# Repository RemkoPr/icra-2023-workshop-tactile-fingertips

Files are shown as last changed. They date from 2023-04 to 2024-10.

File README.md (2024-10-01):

# ICRA2023 Transferability in Robotics Workshop 
## Augmenting Off-the-Shelf Grippers with Tactile Sensing
[Paper](https://doi.org/10.48550/arXiv.2306.05902) -- [Related work](https://doi.org/10.1109/LRA.2023.3284382)

The development of tactile sensing ad its fusion with computer vision is expected to enhance robotic systems in handling complex tasks like deformable object manipulation. However, readily available industrial grippers typically lack tactile feedback, which has led researchers to integrate and develop their own tactile sensors. This has resulted in a wide range of sensor hardware and difficulty in comparing tasksolving performance. We propose moving towards accessible open-source sensors and present a set of fingertips specifically designed for fine object manipulation, with readily interpretable data output. The fingertips are validated through two difficult tasks: cloth edge tracing and cable tracing. 

## Video material
Video material of the proof-of-concept experiments is provided in the videos folder.

## Hardware integration

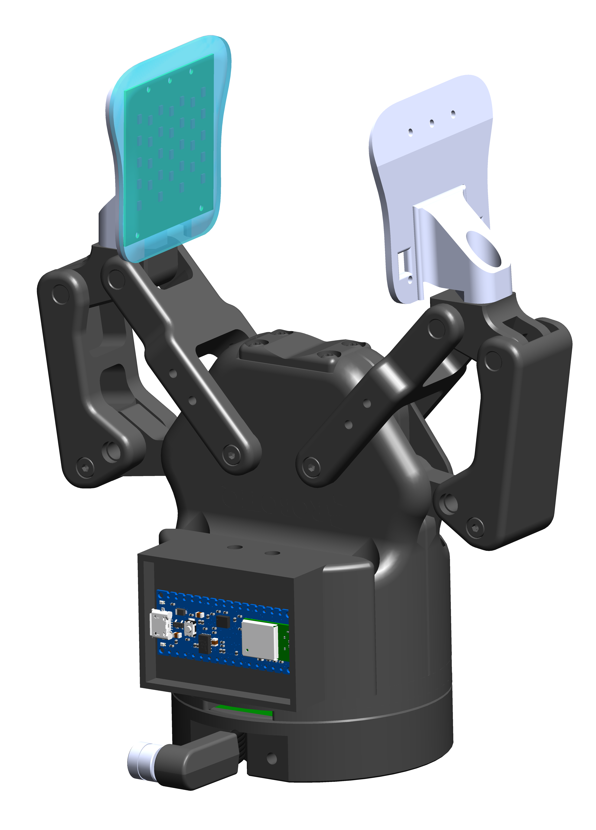
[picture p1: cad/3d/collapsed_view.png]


Currently the fingertips are designed for the Robotiq-2F85 gripper. This gripper can be mounted to various different collaborative robot arms by means of a tool flange. We provide a design for an intermediate flange, nestled between the Robotiq tool flange and the gripper itself, that provides external interfaces for the supply and ground pins otherwise reserved for the gripper. This way, the sensorised fingertips can draw their power straight from the robot arm. The intermediate flange consists of a pcb in the cad/pcb folder and two 3D printed parts in the cad/3d folder. Sensor readout is currently performed by an Arduino Nano 33 BLE externally mounted to the gripper via a 3D printed holder (see cad/3d), but we are in the process of integrating a microcontroller on our custom intermediate flange such that sensor readout and data transmission can also be done internally.  

<BR CLEAR="all">

## Software integration
Both Arduino firmware and python readout software is provided. Data is communicated between the arduino and a remote workstation via Bluetooth Low Energy. Further documentation on the software is provided in the code/python folder.

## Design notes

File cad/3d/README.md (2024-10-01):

This folder contains 3D CAD designs. The solidworks folder contains .sldprt and .sldasm files for editing in SolidWorks. The stl folder contains .stl files for 3D printing without adjustments. The fingertips come in two versions, rigid and flexible. 

The rigid version (IRTouch_rigid) is a single part, best printed face-side up, so that the PCB slot remains smooth. The flex version consists of two parts, where the mechanical interface (IRTouch_flex_interface) is best printed in rigid material. The other part (IRTouch_flex) is printed with Flexfil 98A, face side down, so no support is needed. 

### Note
The files 2F85-OPENED-NO_FINGER.SLDASM and IO_20Coupling_20UR_20CB_20190807.SLDPRT are pulled straight from the [Robotiq Downloads page](https://robotiq.com/cobot-brands/universal-robots).


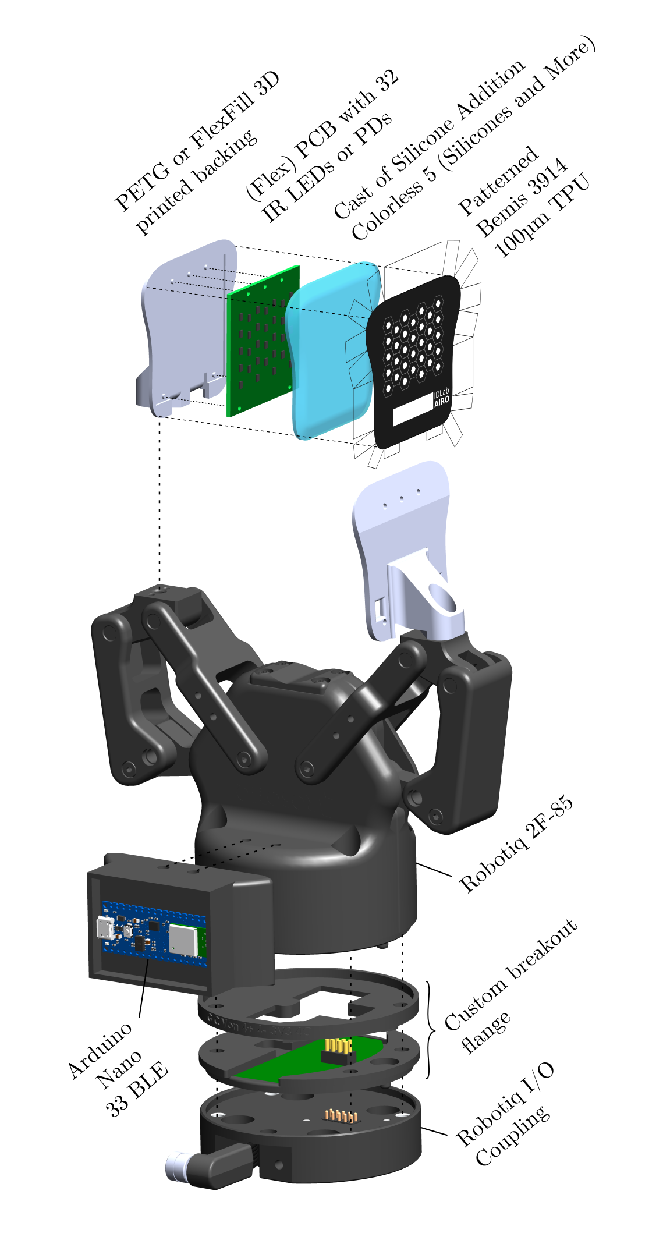
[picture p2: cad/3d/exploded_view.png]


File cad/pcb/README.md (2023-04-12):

This folder contains PCB design files for both the receiver (irtouch_led) as well as the tranmitter (irtouch_rcv) tactile finger. Additionally, the design for the custom breakout flange (robotiq_wrist_coupling) PCB is provided. This PCB is set between the Robotiq I/O Coupling and the 2F-85 gripper itself. The arduino_breakout is a simple PCB to which female 0.1" pin headers are soldered. This PCB fits in the Arduino_holder found in cad/3d.

Refer to the cad/3d folder for an exploded view of the structural integration.

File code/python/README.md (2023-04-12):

# SensorComm

Package allowing communication with IRTouch infrared tactile fingertips, read out using an Arduino nano 33 BLE via Bluetooth Low Energy.

Install using 
```
pip install -e path-to-package-root
```

You may need to install the [TKinter](https://riptutorial.com/tkinter/example/3206/installation-or-setup) module separately. It might be pre-installed, but only for Python2, so make sure it is installed for Python3.
## Note
There's an issue where, if the BLE data characteristic UUID is changed in the Arduino firmware after having already connected to the python script using a different UUID, python may not be able to recongize the new UUID, requiring you to use the old UUID.

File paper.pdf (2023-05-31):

# Augmenting Off-the-Shelf Grippers with Tactile Sensing

1

st Remko Proesmans
IDLab-AIRO
Ghent University – imec
Ghent, Belgium
Remko.Proesmans@UGent.be

2

nd Francis wyffels
IDLab-AIRO
Ghent University – imec
Ghent, Belgium
Francis.wyffels@UGent.be

Abstract—The development of tactile sensing and its fusion with computer vision is expected to enhance robotic systems in handling complex tasks like deformable object manipulation. However, readily available industrial grippers typically lack tactile feedback, which has led researchers to develop and integrate their own tactile sensors. This has resulted in a wide range of sensor hardware, making it difficult to compare performance between different systems. We highlight the value of accessible open-source sensors and present a set of fingertips specifically designed for fine object manipulation, with readily interpretable data outputs. The fingertips are validated through two difficult tasks: cloth edge tracing and cable tracing. Videos of these demonstrations, as well as design files and readout code can be found at https://github.com/RemkoPr/icra-2023-workshop-tactile-fingertips. (https://github.com/RemkoPr/icra-2023-workshop-tactile-fingertips)
Index Terms—Tactile sensing, Sensor-based Control, Open-source
I. INTRODUCTION

Deformable object manipulation challenges several assumptions of classical robotics, like object rigidity, a lowdimensional state space and known dynamics models [1]. Tactile sensing and its fusion with computer vision is expected to strengthen robotic systems in dealing with such complex deformable objects [2]. However, commercially available industrial grippers typically do not feature tactile feedback [3], [4]. At most, binary object detection is included such that delicate parts can be grasped without exerting maximal gripping force. This, combined with force torque sensing in the joints of a robotic arm, is the current extent of readily available tactile feedback. Hence, researchers are required to integrate and even develop their own tactile sensors. Sensor technologies in literature include piezoresistive [5], capacitive [6], thermoelectric [7], optoelectronic [8] and more. This heterogeneity in sensor hardware makes it difficult to compare the performance of control algorithms as the nature of the sensor is strongly intertwined with any control algorithm exploiting it. Few dedicated robotic tactile sensor platforms have been adopted outside their founding research groups. The emphasis of systems that do achieve external adoption, such as robot skins like uSkin [9] and tactile fingertips like GelSight [10],

Remko Proesmans is a predoctoral fellow of the Research Foundation Flanders (FWO) under grant agreement no. 1S15923N. This work was also partially supported by the euROBIn Project (EU grant number 101070596).

is transferability between robotic platforms. These systems aim to be fit for a variety of robots and robotic grippers, so that researchers can acquire tactile add-ons to their pre-owned robotic infrastructure. This hardware transferability facilitates task transferability, mitigating the issue of benchmarking in experiments making use of tactile sensing. GelSight sensors, however, come with considerable overhead in terms of data processing and hardware integration, the latter being due to external cable routing. We argue that there is plenty of room for accessible, open-source tactile fingertips with readily interpretable data outputs. We present a set of narrow fingertips specifically suited for narrow object manipulation and demonstrate their potential in two actively explored problems in the state-of-the-art: cloth edge tracing [11] and cable tracing [8], [12].

II. TACTILE SENSING FOR NARROW OBJECTS

A. Electrical sensor design
The tactile fingers are two complementary designs: one finger emits infrared (IR) light, the other receives it. The fingertips are integrated on a Robotiq 2F-85 gripper, mounted on a UR3e collaborative robot arm. Fig. 1 shows the schematic of the integrated system. The first finger contains a grid of 32 IR light-emitting diodes (LEDs), connected in two parallel branches of each sixteen LEDs. The grid is supplied directly by the 24 V output of the UR3e arm via custom breakout flange between the Robotiq I/O Coupling and the gripper itself. Note that the I/O Coupling, and thus our sensor system, fits a multitude of different cobots and Robotiq grippers. The LED finger consumes 40 mA after a warmup time of five minutes. The second finger consists of 32 IR photodiodes (PDs). Here, four demultiplexers (DEMUX) are included, each addressing eight PDs. The DEMUX are all simultaneously controlled by three digital pins of an Arduino Nano 33 BLE, such that they each route one of four analog pins to one of eight of their respective PDs. In future work, a microcontroller will be integrated on the breakout flange, replacing the externally mounted Arduino. The second finger consumes about 1 mA of current from the 3.3 V output of the Arduino, which in turn receives its power from the 24 V UR3e tool output converted to 5 V by a switching regulator on the breakout flange. The discussed electrical specifications are summarised in Table I.

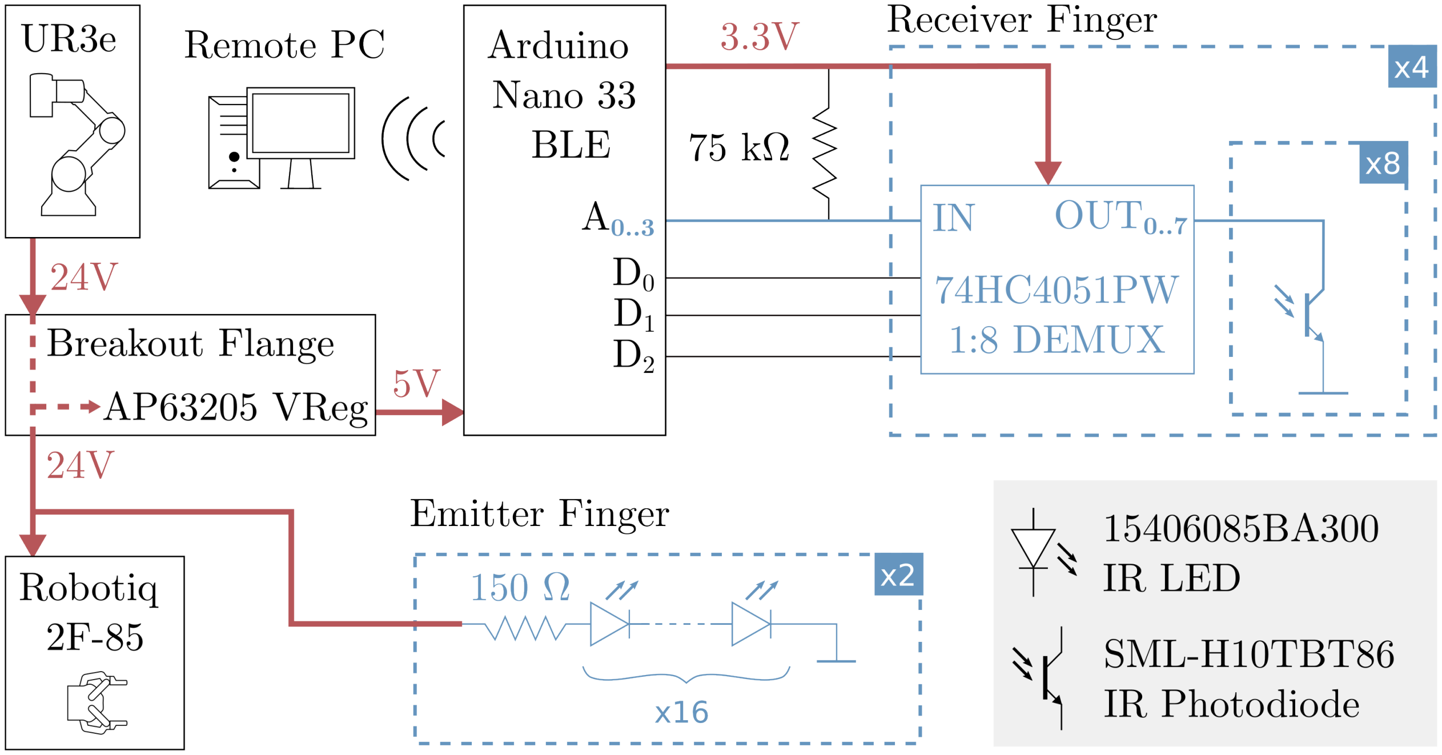
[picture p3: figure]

Fig. 1: Electrical diagram of the tactile fingers integrated on a UR3e.

TABLE I: Technical specifications of the tactile fingers.

Characteristic | Value
Total current consumption (incl. readout) | 45 mA
Receiver finger | 1 mA
Emitter finger | 38 mA
Warmup time | 5 min
Physical size (width × height × depth) | 58.0 × 54.0 × 21 mm³
PCB dimensions | 42.8 × 43.1 mm²
Sensorised area | ∼38.0 × 30.0 mm²
Thickness excluding gripper coupling | 4.0 mm
Sensor density | 3.21 cm⁻²
Data resolution | 8 bit
Readout frequency | 55 Hz

The total current consumption reported includes the voltage regulator and the Arduino during readout.

B. Structural sensor design & manufacturing Structurally, both tactile fingers are largely similar. Fig. 2 shows their constituent parts. The IR LEDs and PDs are each placed in an identical hexagonal grid on their respective printed circuit boards (PCBs), such that a single LED is located straight across from a single PD when both fingers are brought close together. For each finger, the PCB is slotted into a polyethylene terephthalate glycol (PETG) backing, 3D printed using a Prusa MK3 i3. Alternatively, we have succeeded in producing a compliant version by printing the backing with Flexfill TPU 98A and using a flexible PCB. The resulting structure is placed PCB side down into a mould filled with liquid Silicone Addition Colorless 5 obtained from Silicones and More. After curing at room temperature for 24 hours, the finger is removed from the mould and a 1 mm layer of translucent silicone protects the PCB components. We have, however, observed degradation in the polymer right above the IR LEDs after ∼100 grasp cycles, so further material exploration is warranted. However, the surface of this silicone layer is sticky and easily accumulates dirt. Hence, a sheet of 100 µm thick Bemis 3914 thermoplastic polyurethane (TPU) is shaped around the combined PETG, PCB and silicone structure by pulling the TPU taut and heating it locally using a CIF 852 hot air gun set to 90 °C. The TPU was found to provide a low-friction surface for cloth manipulation and is highly

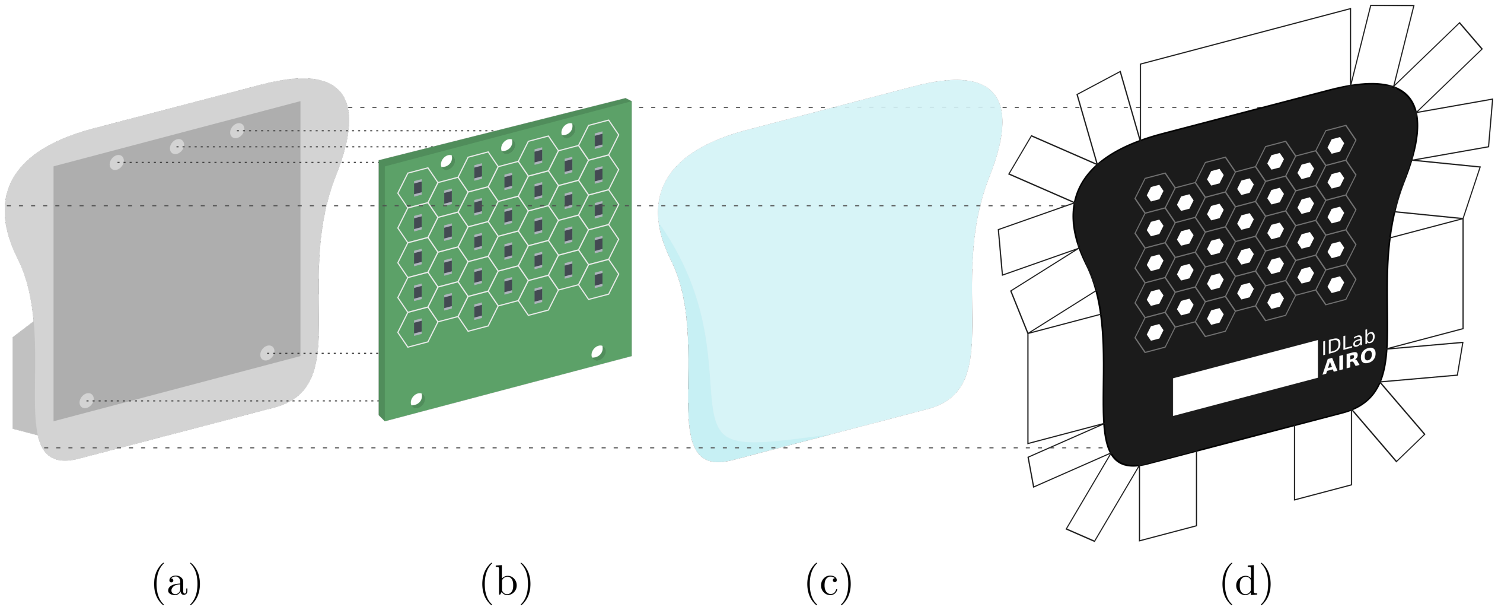
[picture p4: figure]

Fig. 2: Sensor structure for both the emitting as well as the receiving finger. (a) 3D printed PETG backing. (b) PCB, either with 32 IR LEDs or 32 IR PDs. (c) 1.5 mm thick layer of translucent silicone. (d) Sheet of 100 µm Bemis 3914 TPU patterned with black ink.

durable during normal use. Additionally, before shaping, a hole pattern is printed in black on the inside of the TPU layer using an HP LaserJet P2015. Each hole is positioned directly above an IR emitter or receiver, thus focusing their respective radiation patterns. The entire fingertip is 4 mm thick and has a slanted tip, making it suitable for sliding underneath cloth for grasping, as opposed to e.g. GelSight sensors [10]. Table I provides additional structural specifications.

C. Sensor readout
Getting a single readout from the tactile fingers entails sequentially setting the common selection inputs for the DE-MUX to one of eight codes and reading the voltage on the four analog pins that are routed along the receiver grid. This data is transmitted in an 8-bit format at about 55 Hz by the Arduino over Bluetooth Low Energy (BLE). Wireless communication avoids cable routing and thus reduces integration overhead. The use of a widespread communication protocol further encourages transferability.
When the fingers are close together, the PDs receive high IR intensity and pull down the analog pins to ground. Grasped objects between the fingers block a large part of the IR light from the LEDs, which leads to the PDs conducting less and results in higher voltages read by the analog pins. This sensing principle is specifically suited towards, but not limited to, detecting exceedingly narrow objects. Thin cloth, for example, is tough to detect using traditional force sensors. In the following, the 8-bit complement of the readings is reported, as it is more intuitive that high IR light transmission corresponds to high sensor readings.

III. EXPERIMENTAL VALIDATION

A. Response to different materials
The sensor readout depends on the translucency of the material that is grasped. Fig. 3 shows the average 8-bit value received by the PD grid when placing different materials between the fingertips at a separation distance of 6 mm. The materials are solid cardboard, a pink hand towel, a sheet of white paper, a thin white cloth napkin and a clear plastic ziplock bag. The results are intuitively clear: more translucent materials lead to higher sensor readings.

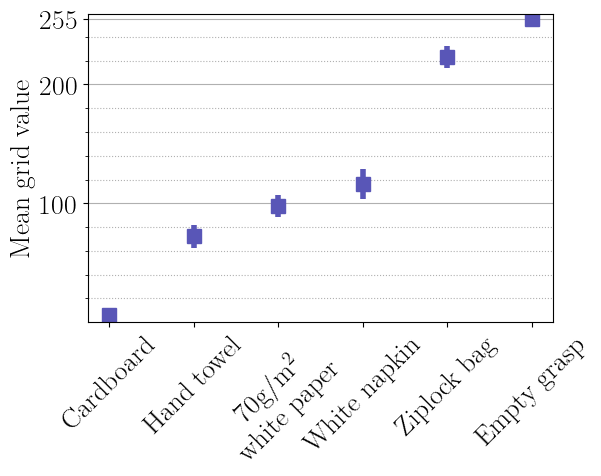
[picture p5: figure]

Fig. 3: Mean sensor values when grasping different materials.

B. Task solving

The sensors are validated in two actively explored problems in the state-of-the-art: cloth edge tracing (Fig. 4a-4d) and cable tracing (Fig. 4e-4f). The used methods are directly transferable to other robotic installations to which the fingertips can be fitted. We refer the reader to the accompanying GitHub page for video material.
The tactile data is distilled into a set of control parameters as follows. Each data value corresponds to a hexagonal cell, of which the position in the grid is defined by its centre coordinates. In most use cases, the grid will show distinct dark and bright zones, see the visualisations in Fig. 4. Several processing steps are applied to the sensor data:
- The threshold λ deciding which values are “bright”, respectively “dark”, is calculated by sorting all grid values from lowest to highest and finding the largest step between adjacent values. Any values found before this step are “dark”, the others “bright”. λ is then set to the average of the bright cluster mean and the dark cluster mean value.
- The centre point of the dark cluster is calculated as the weighted mean of the centre coordinates of all cells belonging to the dark cluster, where the weights are the 8-bit complements of the associated values.
- The shape of the border between the dark and the bright cluster indicates whether or not a corner is grasped when tracing cloth, or shows the angle at which the cable is passing through the fingers. To find the border shape, the value of each cell is compared to those of the neighbouring cells. If λ is crossed between cells, the values of the cells are linearly interpolated along the line segment connecting the cell centre points and an edge marker is placed where an interpolated value of λ is found. Piecewise linear functions are then fitted to these edge markers.

In both experiments, proportional control with manually tuned gain is used to maintain the centre point of the dark cluster at a certain height in the sensor grid.

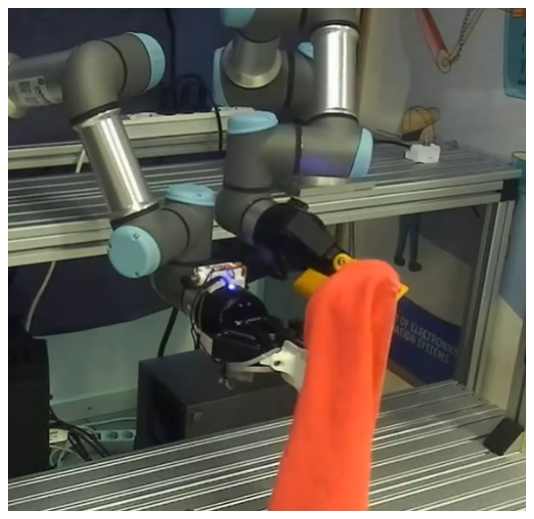
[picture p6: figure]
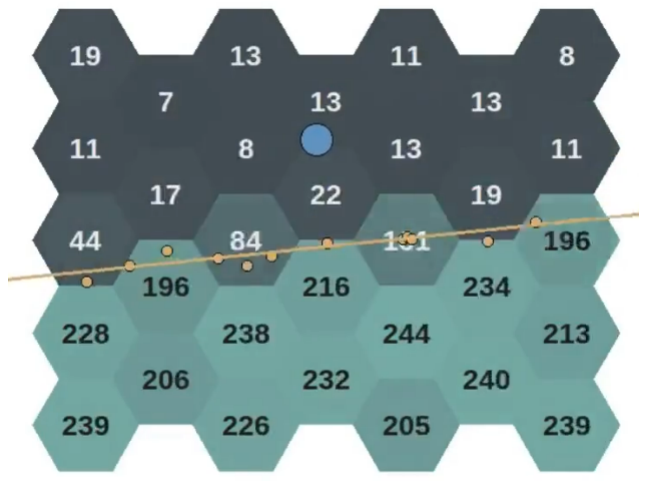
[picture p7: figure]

(a) Grasping cloth edge. (b) Sensor values corresponding to Fig. 4a.

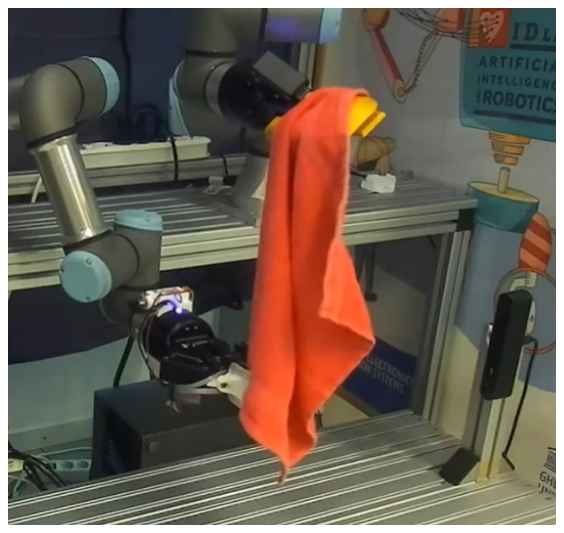
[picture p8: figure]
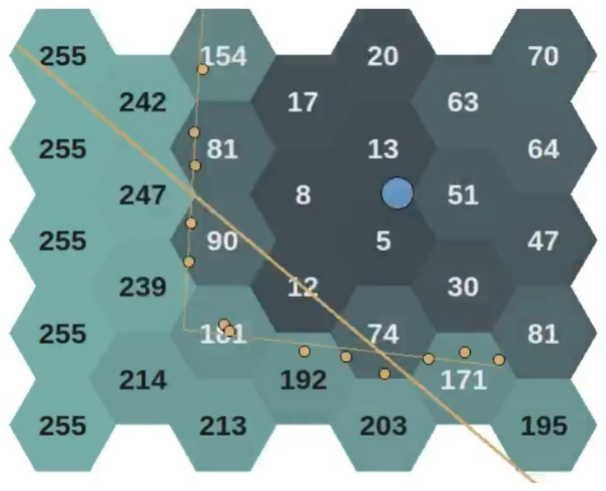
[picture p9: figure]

(c) Grasping cloth corner. (d) Sensor values corresponding to Fig. 4c.

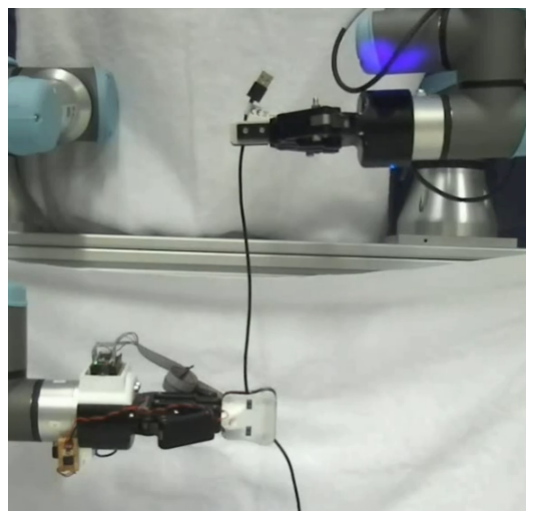
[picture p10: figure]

(e) Grasping 3 mm USB cable.

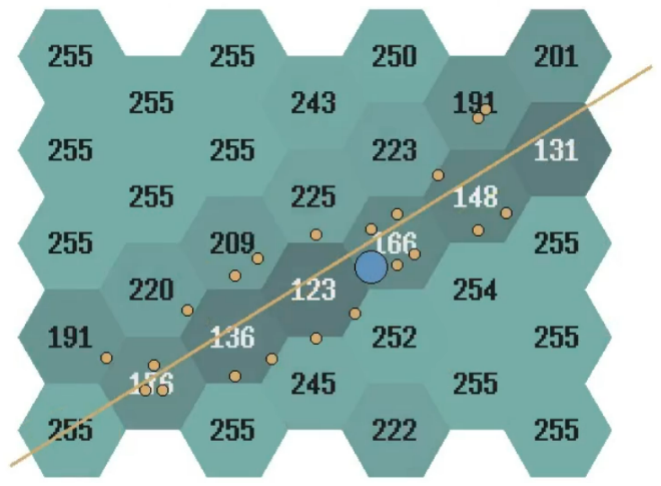
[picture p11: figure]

(f) Sensor values corresponding to Fig. 4e.

Fig. 4: Cloth and cable tracing.

IV. CONCLUSION

Transferability in robotics is strongly hardware-limited. In the field of tactile sensing, a mitigating approach is to design tactile fingertips, facilitating transfer of such sensors between heterogeneous robotic hardware and potentially allowing for direct control policy transferability. We have presented a set of open-source optoelectronic tactile fingertips and have demonstrated their potential in cable and cloth edge tracing. The tactile fingertips are uniquely suited towards manipulation of narrow objects, while being thinner than e.g. GelSight sensors and the optoelectronic sensors in [8], allowing for a compliant design. Additionally, sensor platforms like ours are more accessible than GelSight sensors in terms of cost and both hardware and software integration, further incentivising benchmarking in tactile robotics.

REFERENCES

[1] J. Zhu et al., ”Challenges and Outlook in Robotic Manipulation of Deformable Objects,” in IEEE Robotics & Automation Magazine, vol. 29, no. 3, pp. 67-77, Sept. 2022.
[2] A. Billard, and D. Kragic, ”Trends and challenges in robot manipulation,” in Science, vol. 364, no. 6446, pp. eaat8414, June 2019.
[3] J. Borras, G. Aleny ` | a and C. Torras, ”A grasping-centered analysis for `
cloth manipulation,” in IEEE Transactions on Robotics, vol. 36, no. 3, pp. 924-936, June 2020.
[4] L. Birglen, and T. Schlicht, ”A statistical review of industrial robotic grippers,” in Robotics and Computer-Integrated Manufacturing, vol. 49, pp. 88-97, February 2018.
[5] L. Zlokapa et al., ”An integrated design pipeline for tactile sensing robotic manipulators,” International Conference on Robotics and Automation (ICRA), pp. 3136-3142, April 2022.
[6] E. J. K. Judd, B. Aksoy, K. M. Digumarti, H. Shea, and D. Floreano, ”Slip anticipation for grasping deformable objects using a soft force sensor,” in International Conference on Intelligent Robots and Systems (IROS), October 2022.
[7] G. Li, S. Liu, L. Wang, and R. Zhu, ”Skin-inspired quadruple tactile sensors integrated on a robot hand enable object recognition,” in Science Robotics, vol. 5, no. 49, December 2020.
[8] A. Cirillo, M. Costanzo, G. Laudante, and S. Pirozzi, ”Tactile sensors for parallel grippers: design and characterization,” in Sensors, vol. 21, no. 5, p. 1915, March 2021.
[9] T. P. Tomo et al., ”A new silicone structure for uSkin—a soft, distributed, digital 3-axis skin sensor and its integration on the humanoid robot iCub,” in IEEE Robotics and Automation Letters, vol. 3, no. 3, pp. 2584-2591, July 2018.
[10] M. Lambeta et al., ”DIGIT: A novel design for a low-cost compact high-resolution tactile sensor with application to in-hand manipulation,” in IEEE Robotics and Automation Letters, vol. 5, no. 3, pp. 3838-3845, July 2020.
[11] N. Sunil, S. Wang, Y. She, E. Adelson, and A. Rodriguez, ”Visuotactile Affordances for Cloth Manipulation with Local Control,” in Conference on Robot Learning (CoRL), December 2022.
[12] Y. She, S. Wang, N. Sunil, A. Rodriguez, and E. Adelson, ”Cable manipulation with a tactile-reactive gripper,” in Int. J. Robot. Res. (IJRR), vol. 40, no. 12-14, pp. 1385-1401, August 2021.

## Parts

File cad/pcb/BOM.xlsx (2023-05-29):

 | Component | Manufacturer part number | Quantity | PCB designation
Receiver finger
 | infrared photodiode | SML-H10TBT86 | 32 | Q1-32
 | 1-to-8 demultiplexer | 74HC4051PW | 4 | U1-4
 | pull-down resistor | any 75kOhm 0603 1/16W | 4 | R1-4
Transmitter finger
 | infrared LED | 15406085BA300 | 32 | D1-32
 | current limiting resistor | any 150 Ohm 0603 1/10W | 2 | R3, R8
Breakout flange
 | pogo pin header | 827-22-010-10-001101 | 1 | U12
 | 7 position box header | any 90° 2,54mm pitch 7-positiion box header | 2
 | 5V switching regulator | AP63205 | 1 | IC1
 | decoupling capacitor | any 0805 22µF capacitor | 2 | C3, C4
 | decoupling capacitor | any 0603 10µF 30V rated capacitor | 1 | C1
 | decoupling capacitor | any 0603 100nF capacitor | 1 | C2
 | inductor | any 0603 4,7µH inductor | 1 | L1

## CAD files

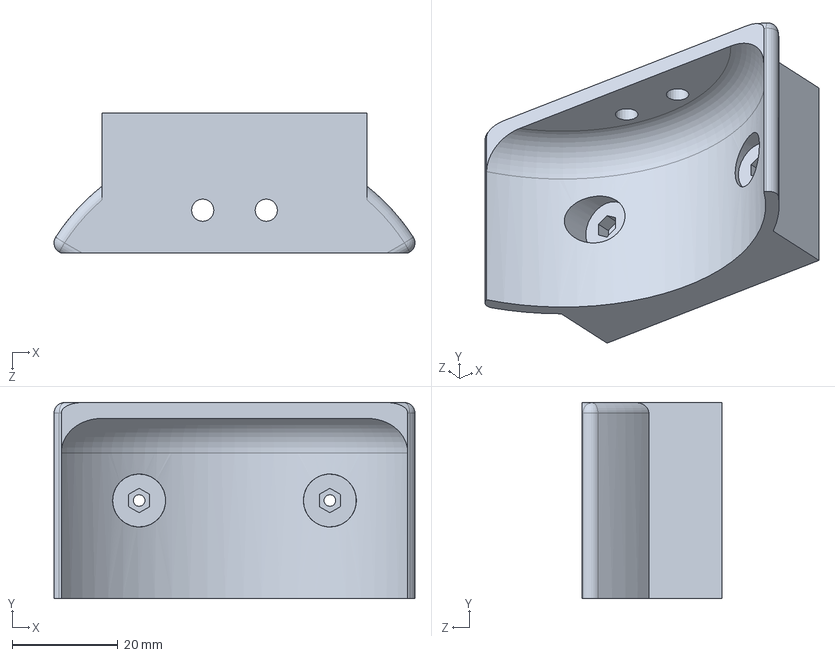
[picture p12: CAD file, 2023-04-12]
cad/3d/solidworks/Arduino_holder.SLDPRT
68.1 x 37.0 x 26.5 mm

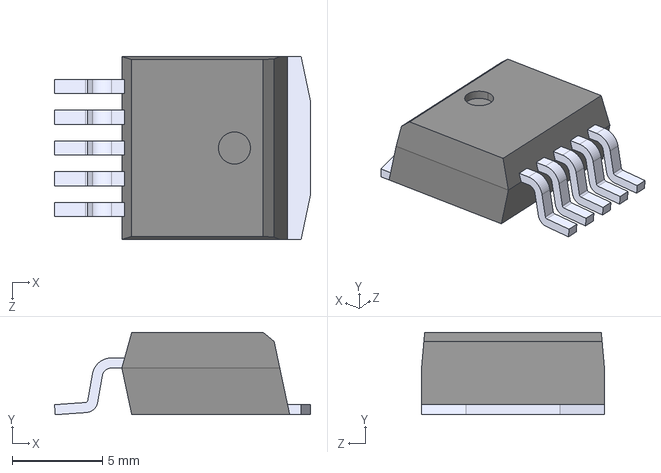
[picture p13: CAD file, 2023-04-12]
cad/pcb/irtouch_lib/LM2576D2TR4-012G.step
14.2 x 4.57 x 10.1 mm

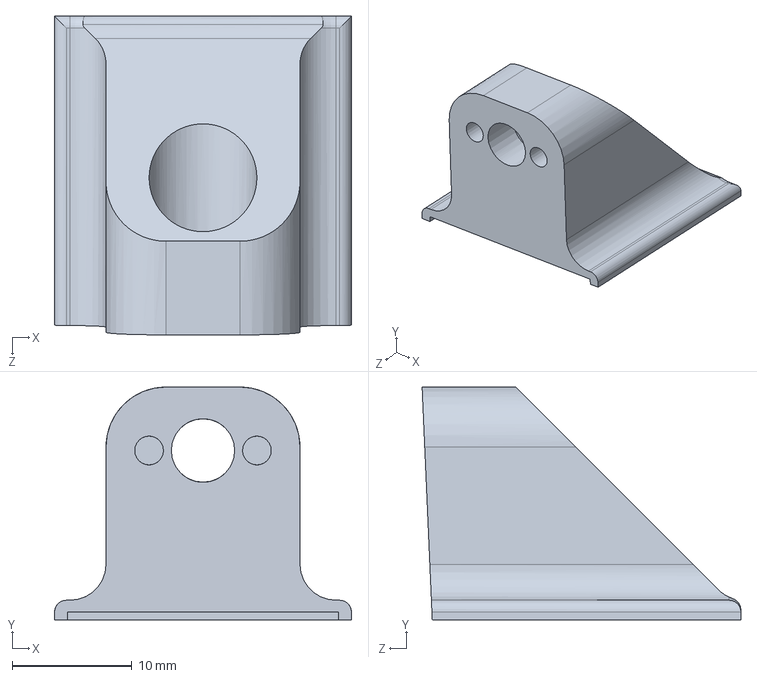
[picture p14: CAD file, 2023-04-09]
cad/3d/solidworks/IRTouch_flex_interface_base.SLDPRT
24.8 x 19.4 x 26.6 mm

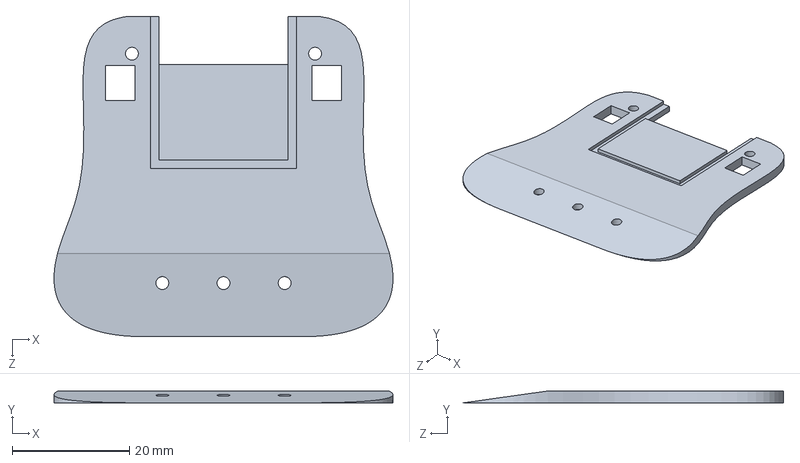
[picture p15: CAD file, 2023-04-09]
cad/3d/solidworks/IRTouch_flex.SLDPRT
57.9 x 2.00 x 54.7 mm

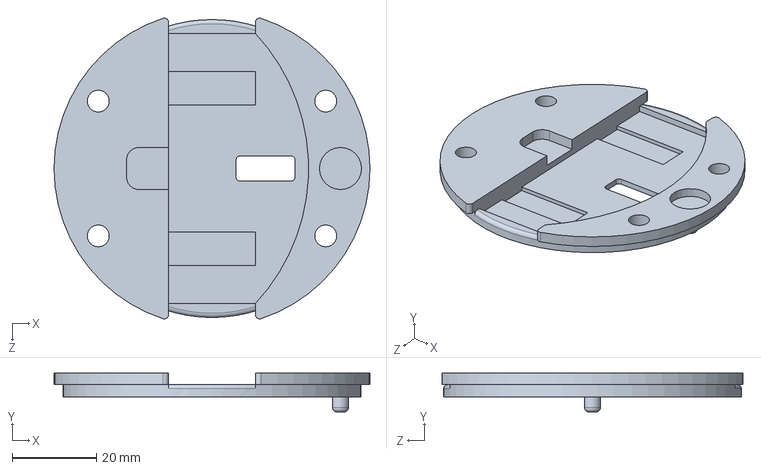
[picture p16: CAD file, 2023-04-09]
cad/3d/solidworks/PCB_flange.SLDPRT
75.0 x 9.20 x 71.4 mm

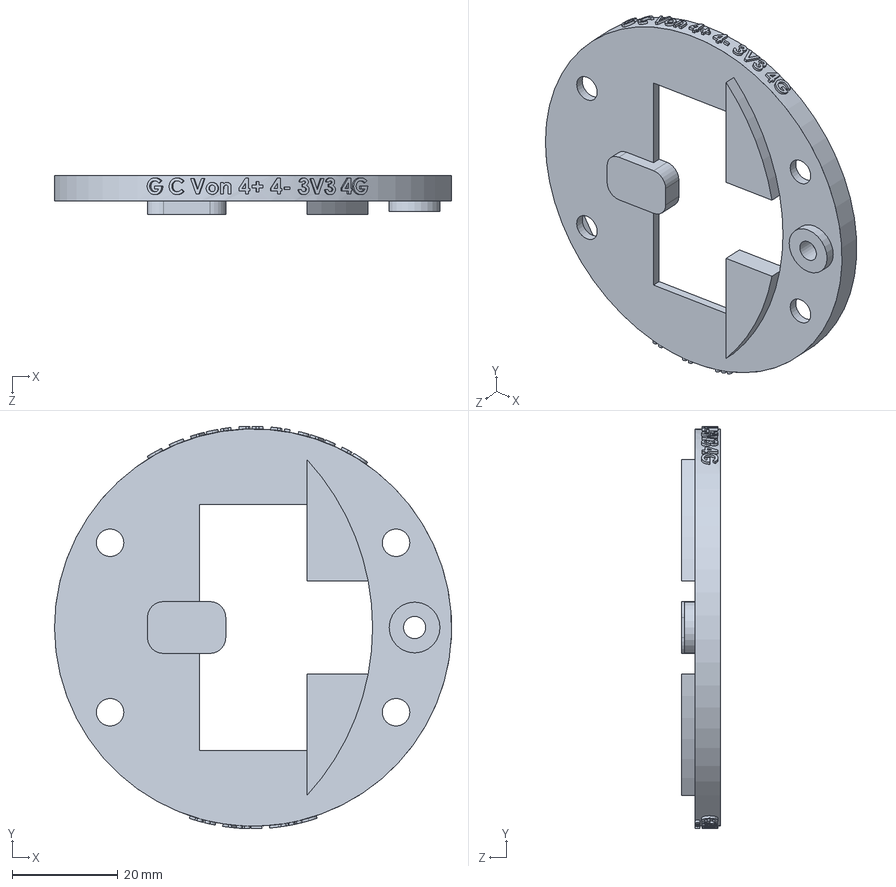
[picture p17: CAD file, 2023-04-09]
cad/3d/solidworks/PCB_flange_top.SLDPRT
75.0 x 76.0 x 7.30 mm

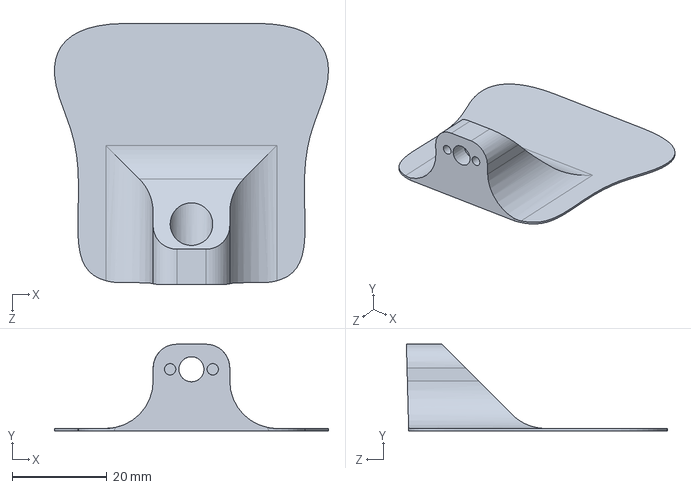
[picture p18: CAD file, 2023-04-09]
cad/3d/solidworks/IRTouch_rigid_base.SLDPRT
57.9 x 18.3 x 55.2 mm

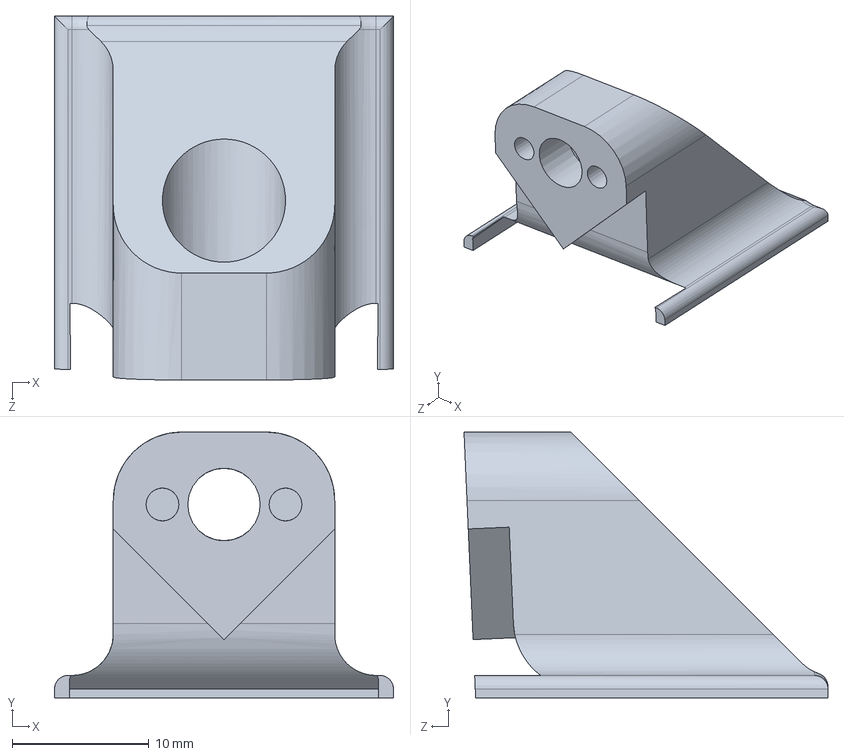
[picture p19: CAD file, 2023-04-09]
cad/3d/solidworks/IRTouch_flex_interface.SLDPRT
24.8 x 19.4 x 26.6 mm

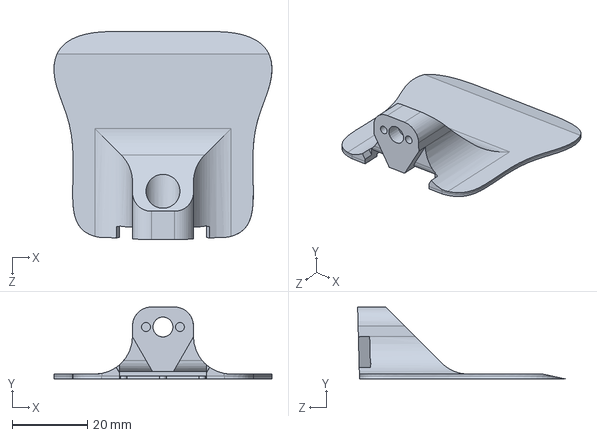
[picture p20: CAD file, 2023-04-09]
cad/3d/solidworks/IRTouch_rigid.SLDPRT
57.9 x 19.1 x 55.2 mm

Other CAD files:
cad/3d/stl/Arduino_holder.STL
cad/3d/stl/IRTouch_flex.STL
cad/3d/stl/IRTouch_flex_interface.STL
cad/3d/stl/IRTouch_rigid.STL
cad/3d/stl/PCB_flange.STL
cad/3d/stl/PCB_flange_top.STL

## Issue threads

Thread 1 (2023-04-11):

Redo RCV PCB to multiplex series resistors

RemkoPr, 2023-04-11:
Currently, each infrared photodiode has a series pullup resistor. This is unnecessary: the resistor can be placed before the multiplexer, such that only 4 are needed instead of 32. This should also allow to turn the receiver PCB into a 2-layer design.

Closed 2023-05-11.

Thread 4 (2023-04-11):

Rework breakout flange to include microcontroller

RemkoPr, 2023-04-11:
The breakout flange currently only provides access to the pins used by the Robotiq 2F-85. We aim to integrate a microcontroller on this flange as well, such that the external Arduino can be replaced.

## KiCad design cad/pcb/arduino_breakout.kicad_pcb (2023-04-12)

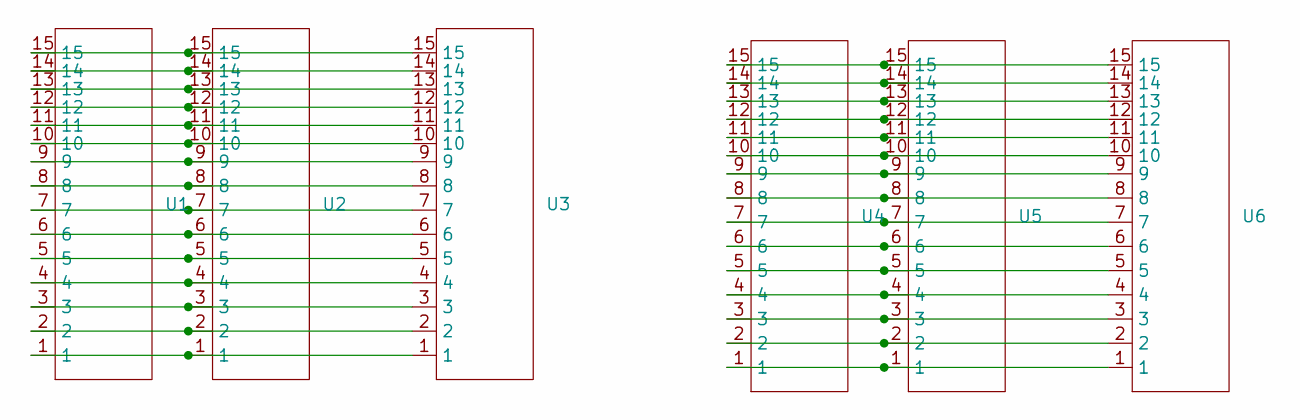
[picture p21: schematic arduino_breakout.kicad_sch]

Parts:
U1, U2, U3, U4, U5, U6: 15POS_INTERFACE

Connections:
unnamed: U1.1, U2.1, U3.1
unnamed: U1.2, U2.2, U3.2
unnamed: U1.3, U2.3, U3.3
unnamed: U1.4, U2.4, U3.4
unnamed: U1.5, U2.5, U3.5
unnamed: U1.6, U2.6, U3.6
unnamed: U1.7, U2.7, U3.7
unnamed: U1.8, U2.8, U3.8
unnamed: U1.9, U2.9, U3.9
unnamed: U1.10, U2.10, U3.10
unnamed: U1.11, U2.11, U3.11
unnamed: U1.12, U2.12, U3.12
unnamed: U1.13, U2.13, U3.13
unnamed: U1.14, U2.14, U3.14
unnamed: U1.15, U2.15, U3.15
unnamed: U4.1, U5.1, U6.1
unnamed: U4.2, U5.2, U6.2
unnamed: U4.3, U5.3, U6.3
unnamed: U4.4, U5.4, U6.4
unnamed: U4.5, U5.5, U6.5
unnamed: U4.6, U5.6, U6.6
unnamed: U4.7, U5.7, U6.7
unnamed: U4.8, U5.8, U6.8
unnamed: U4.9, U5.9, U6.9
unnamed: U4.10, U5.10, U6.10
unnamed: U4.11, U5.11, U6.11
unnamed: U4.12, U5.12, U6.12
unnamed: U4.13, U5.13, U6.13
unnamed: U4.14, U5.14, U6.14
unnamed: U4.15, U5.15, U6.15

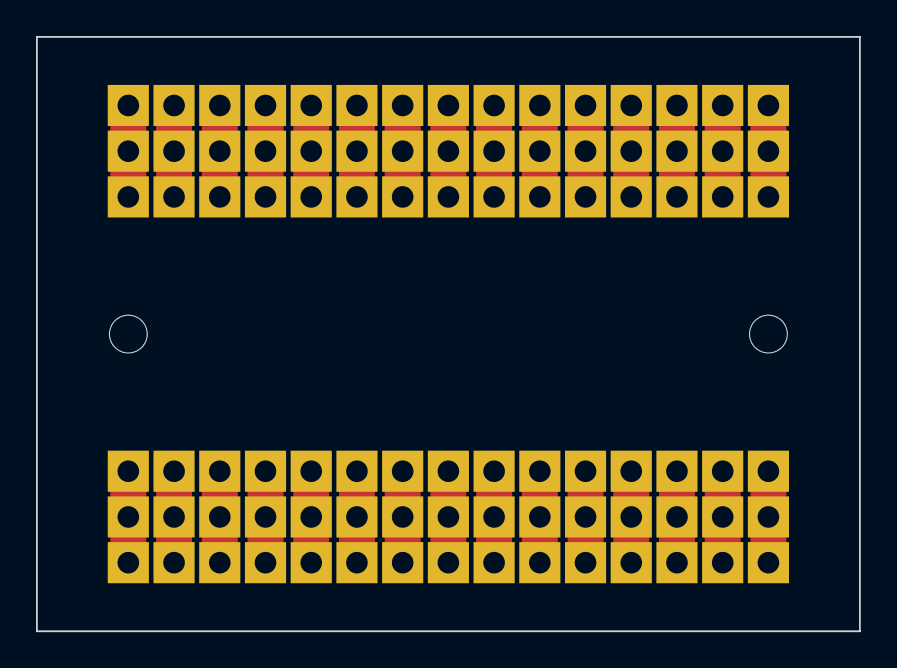
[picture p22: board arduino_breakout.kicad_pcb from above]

Board: 2 copper layers, 45.7 x 33.0 mm, 6 parts (0 on the bottom side), 30 nets.

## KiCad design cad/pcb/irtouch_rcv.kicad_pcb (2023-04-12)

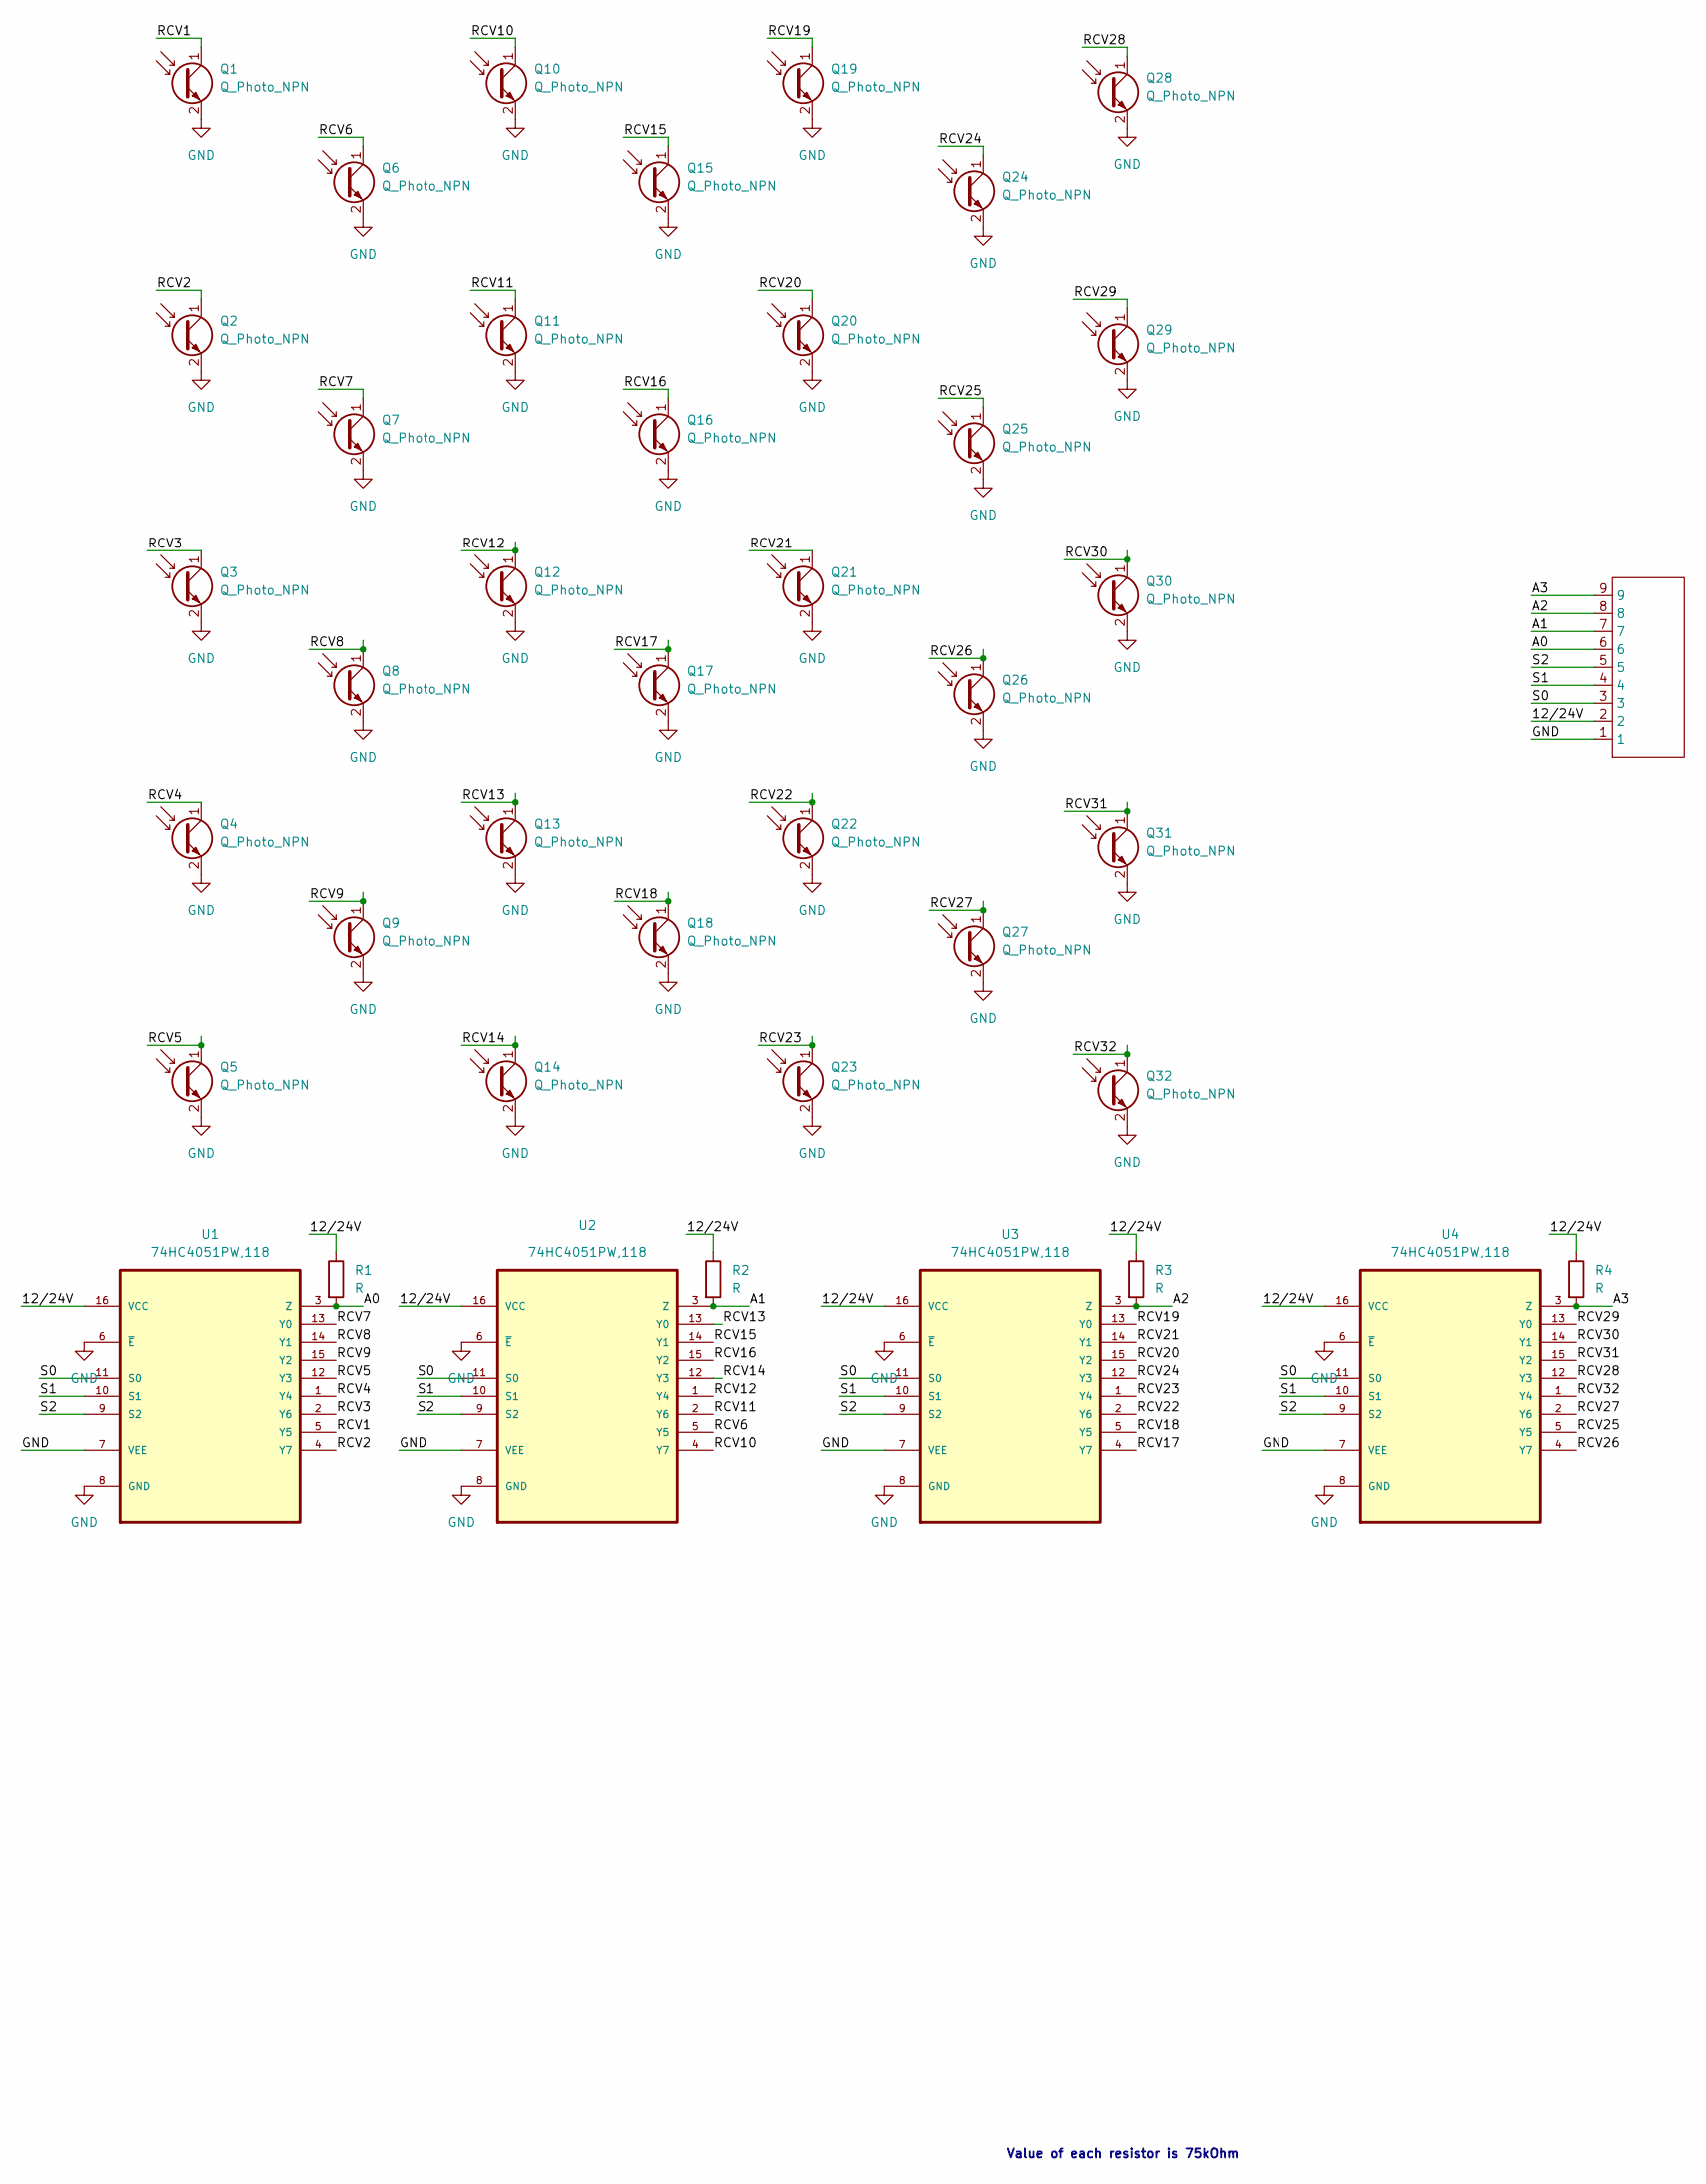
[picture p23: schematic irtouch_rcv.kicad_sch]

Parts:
I1: 9POS_INTERFACE
Q1, Q2, Q3, Q4, Q5, Q6, Q7, Q8, Q9, Q10, Q11, Q12, Q13, Q14, Q15, Q16, Q17, Q18, Q19, Q20, Q21, Q22, Q23, Q24, Q25, Q26, Q27, Q28, Q29, Q30, Q31, Q32: Q_Photo_NPN; RCVR
R1, R2, R3, R4: R; R0603
U1, U2, U3, U4: 74HC4051PW,118; SOP65P640X110-16N; MPN 74HC4051PW,118

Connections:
/12/24V: I1.2, R1.1, R2.1, R3.1, R4.1, U1.16 (VCC), U2.16 (VCC), U3.16 (VCC), U4.16 (VCC)
/A0: I1.6, R1.2, U1.3 (Z)
/A1: I1.7, R2.2, U2.3 (Z)
/A2: I1.8, R3.2, U3.3 (Z)
/A3: I1.9, R4.2, U4.3 (Z)
/RCV1: Q1.1 (C), U1.5 (Y5)
/RCV2: Q2.1 (C), U1.4 (Y7)
/RCV3: Q3.1 (C), U1.2 (Y6)
/RCV4: Q4.1 (C), U1.1 (Y4)
/RCV5: Q5.1 (C), U1.12 (Y3)
/RCV6: Q6.1 (C), U2.5 (Y5)
/RCV7: Q7.1 (C), U1.13 (Y0)
/RCV8: Q8.1 (C), U1.14 (Y1)
/RCV9: Q9.1 (C), U1.15 (Y2)
/RCV10: Q10.1 (C), U2.4 (Y7)
/RCV11: Q11.1 (C), U2.2 (Y6)
/RCV12: Q12.1 (C), U2.1 (Y4)
/RCV13: Q13.1 (C), U2.13 (Y0)
/RCV14: Q14.1 (C), U2.12 (Y3)
/RCV15: Q15.1 (C), U2.14 (Y1)
/RCV16: Q16.1 (C), U2.15 (Y2)
/RCV17: Q17.1 (C), U3.4 (Y7)
/RCV18: Q18.1 (C), U3.5 (Y5)
/RCV19: Q19.1 (C), U3.13 (Y0)
/RCV20: Q20.1 (C), U3.15 (Y2)
/RCV21: Q21.1 (C), U3.14 (Y1)
/RCV22: Q22.1 (C), U3.2 (Y6)
/RCV23: Q23.1 (C), U3.1 (Y4)
/RCV24: Q24.1 (C), U3.12 (Y3)
/RCV25: Q25.1 (C), U4.5 (Y5)
/RCV26: Q26.1 (C), U4.4 (Y7)
/RCV27: Q27.1 (C), U4.2 (Y6)
/RCV28: Q28.1 (C), U4.12 (Y3)
/RCV29: Q29.1 (C), U4.13 (Y0)
/RCV30: Q30.1 (C), U4.14 (Y1)
/RCV31: Q31.1 (C), U4.15 (Y2)
/RCV32: Q32.1 (C), U4.1 (Y4)
/S0: I1.3, U1.11 (S0), U2.11 (S0), U3.11 (S0), U4.11 (S0)
/S1: I1.4, U1.10 (S1), U2.10 (S1), U3.10 (S1), U4.10 (S1)
/S2: I1.5, U1.9 (S2), U2.9 (S2), U3.9 (S2), U4.9 (S2)
GND: I1.1, Q1.2 (E), Q2.2 (E), Q3.2 (E), Q4.2 (E), Q5.2 (E), Q6.2 (E), Q7.2 (E), Q8.2 (E), Q9.2 (E), Q10.2 (E), Q11.2 (E), Q12.2 (E), Q13.2 (E), Q14.2 (E), Q15.2 (E), Q16.2 (E), Q17.2 (E), Q18.2 (E), Q19.2 (E), Q20.2 (E), Q21.2 (E), Q22.2 (E), Q23.2 (E), Q24.2 (E), Q25.2 (E), Q26.2 (E), Q27.2 (E), Q28.2 (E), Q29.2 (E), Q30.2 (E), Q31.2 (E), Q32.2 (E), U1.6 (~E), U1.7 (VEE), U1.8 (GND), U2.6 (~E), U2.7 (VEE), U2.8 (GND), U3.6 (~E), U3.7 (VEE), U3.8 (GND), U4.6 (~E), U4.7 (VEE), U4.8 (GND)

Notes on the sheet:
Value of each resistor is 75kOhm

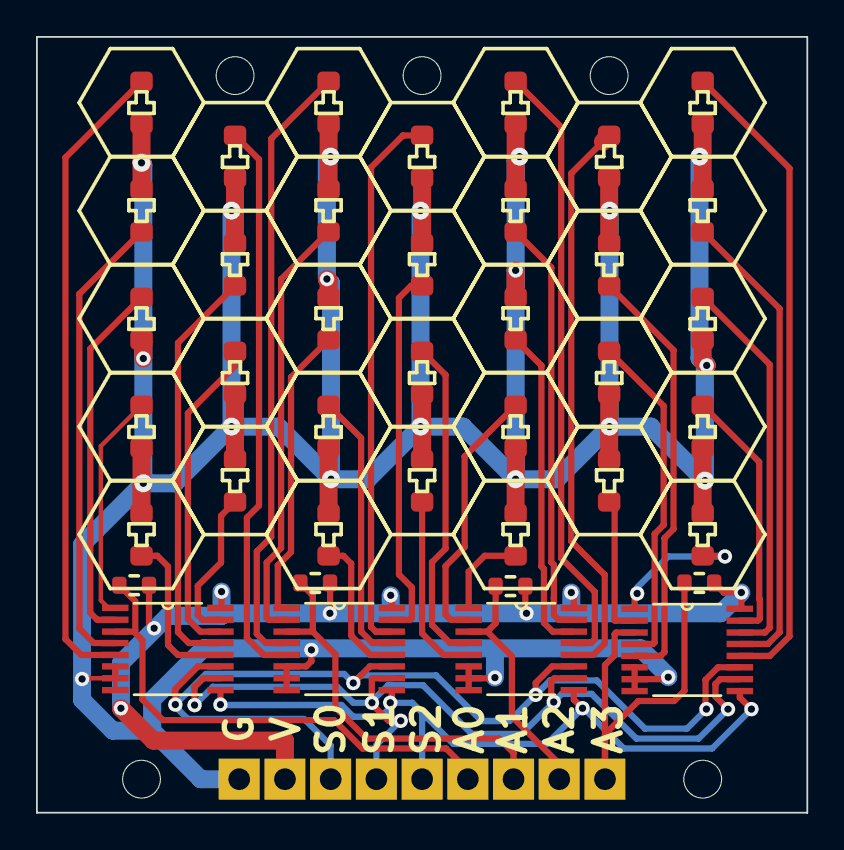
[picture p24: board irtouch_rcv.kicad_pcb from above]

Board: 4 copper layers, 42.8 x 43.1 mm, 41 parts (0 on the bottom side), 41 nets.

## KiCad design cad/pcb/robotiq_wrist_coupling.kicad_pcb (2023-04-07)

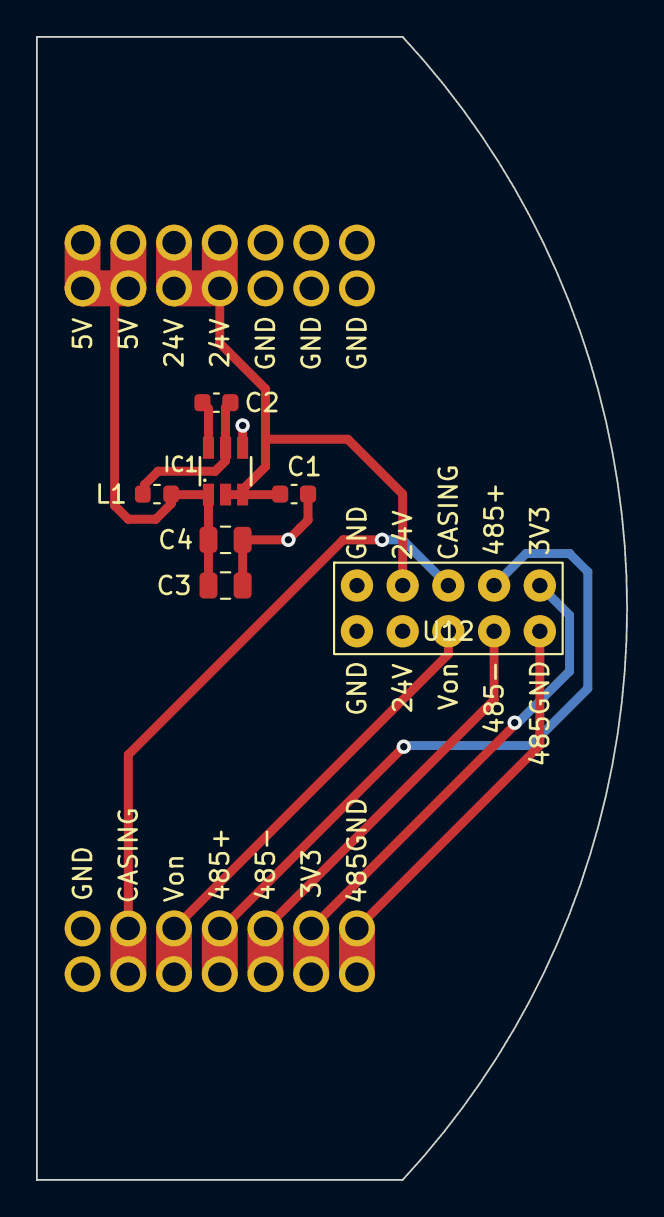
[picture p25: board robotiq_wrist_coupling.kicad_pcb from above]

Board: 2 copper layers, 32.8 x 63.5 mm, 35 parts (0 on the bottom side), 11 nets.

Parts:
C1: 10µF; C_0603_1608Metric
C2: 100nF; C_0603_1608Metric
C3, C4: 22µF; C_0805_2012Metric
IC1: AP63205; TSOT23-6
L1: 4µ7; L_0603_1608Metric
U1, U2, U2#2, U3, U3#2, U4, U5, U5#2, U6, U7, U8, U9, U10, U11, U13, U14, U15, U15#2, U16, U16#2, U17, U18, U19, U20, U21, U21#2, U22, U22#2: HOLE
U12: 10PIN_SPRING_HEADER

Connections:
/3V3_out: U10.1, U11.1, U12.9
/5V: C3.1, C4.1, IC1.1 (FB), L1.2, U21.1, U21#2.1, U22.1, U22#2.1
/24V: C1.1, IC1.2 (EN), IC1.3 (VIN), U12.3, U15.1, U15#2.1, U16.1, U16#2.1
/485+: U8.1, U9.1, U12.7
/485-: U12.8, U14.1, U18.1
/485GND: U12.10, U19.1, U20.1
/CASING: U6.1, U7.1, U12.5
/Von: U12.6, U13.1, U17.1
GND: C1.2, C3.2, C4.2, IC1.4 (GND), U1.1, U2.1, U2#2.1, U3.1, U3#2.1, U4.1, U5.1, U5#2.1, U12.1, U12.2
unnamed: C2.1, IC1.6 (BST)
unnamed: C2.2, IC1.5 (SW), L1.1

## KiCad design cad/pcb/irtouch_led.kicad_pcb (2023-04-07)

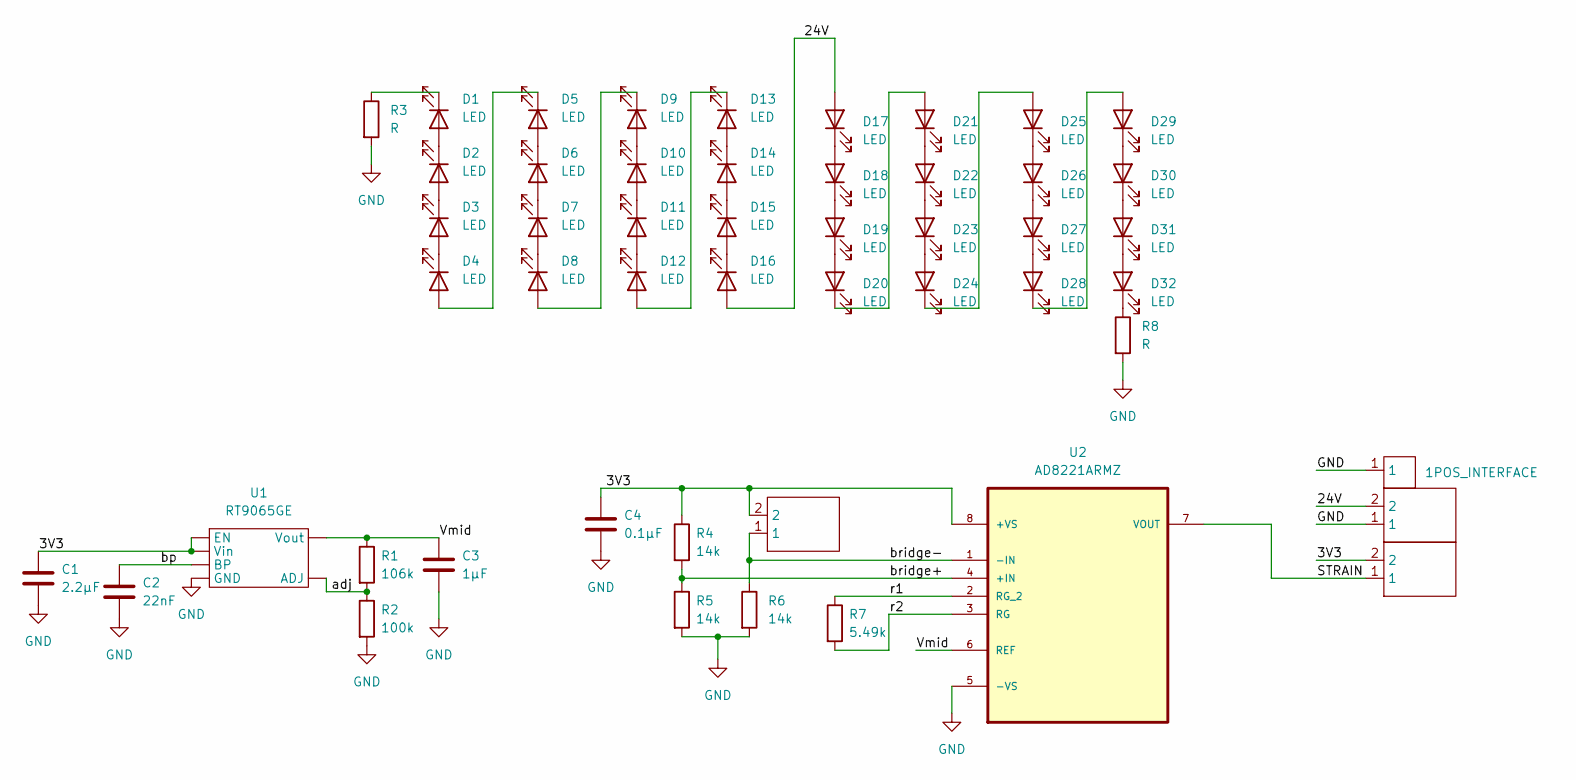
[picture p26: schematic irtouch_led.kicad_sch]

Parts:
C1: 2.2µF; C_0603_1608Metric
C2: 22nF; C_0603_1608Metric
C3: 1µF; C_0603_1608Metric
C4: 0.1µF; C_0603_1608Metric
D1, D2, D3, D4, D5, D6, D7, D8, D9, D10, D11, D12, D13, D14, D15, D16, D17, D18, D19, D20, D21, D22, D23, D24, D25, D26, D27, D28, D29, D30, D31, D32: LED; LED0603
I1: 2POS_INTERFACE; 2POS_STRAIN_INTERFACE
I2, I3: 2POS_INTERFACE
R1: 106k; R_0603_1608Metric
R2: 100k; R_0603_1608Metric
R3, R8: R; R_0603_1608Metric
R4, R5, R6: 14k; R_0603_1608Metric
R7: 5.49k; R_0603_1608Metric
U1: RT9065GE; SOT-23-6
U2: AD8221ARMZ; SOP65P490X110-8N; MPN AD8221ARMZ
U3: 1POS_INTERFACE

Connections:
/3V3: C1.1, C4.1, I1.2, I3.2, R4.1, U1.1 (Vin), U1.3 (EN), U2.8 (+VS)
/24V: D16.2 (A), D17.2 (A), I2.2
/STRAIN: I3.1, U2.7 (VOUT)
/Vmid: C3.1, R1.1, U1.6 (Vout), U2.6 (REF)
/adj: R1.2, R2.1, U1.5 (ADJ)
/bp: C2.1, U1.4 (BP)
/bridge+: R4.2, R5.1, U2.4 (+IN)
/bridge-: I1.1, R6.1, U2.1 (-IN)
/r1: R7.1, U2.2 (RG_2)
/r2: R7.2, U2.3 (RG)
GND: C1.2, C2.2, C3.2, C4.2, I2.1, R2.2, R3.2, R5.2, R6.2, R8.2, U1.2 (GND), U2.5 (-VS), U3.1
unnamed: D1.1 (K), R3.1
unnamed: D1.2 (A), D2.1 (K)
unnamed: D2.2 (A), D3.1 (K)
unnamed: D3.2 (A), D4.1 (K)
unnamed: D4.2 (A), D5.1 (K)
unnamed: D5.2 (A), D6.1 (K)
unnamed: D6.2 (A), D7.1 (K)
unnamed: D7.2 (A), D8.1 (K)
unnamed: D8.2 (A), D9.1 (K)
unnamed: D9.2 (A), D10.1 (K)
unnamed: D10.2 (A), D11.1 (K)
unnamed: D11.2 (A), D12.1 (K)
unnamed: D12.2 (A), D13.1 (K)
unnamed: D13.2 (A), D14.1 (K)
unnamed: D14.2 (A), D15.1 (K)
unnamed: D15.2 (A), D16.1 (K)
unnamed: D17.1 (K), D18.2 (A)
unnamed: D18.1 (K), D19.2 (A)
unnamed: D19.1 (K), D20.2 (A)
unnamed: D20.1 (K), D21.2 (A)
unnamed: D21.1 (K), D22.2 (A)
unnamed: D22.1 (K), D23.2 (A)
unnamed: D23.1 (K), D24.2 (A)
unnamed: D24.1 (K), D25.2 (A)
unnamed: D25.1 (K), D26.2 (A)
unnamed: D26.1 (K), D27.2 (A)
unnamed: D27.1 (K), D28.2 (A)
unnamed: D28.1 (K), D29.2 (A)
unnamed: D29.1 (K), D30.2 (A)
unnamed: D30.1 (K), D31.2 (A)
unnamed: D31.1 (K), D32.2 (A)
unnamed: D32.1 (K), R8.1

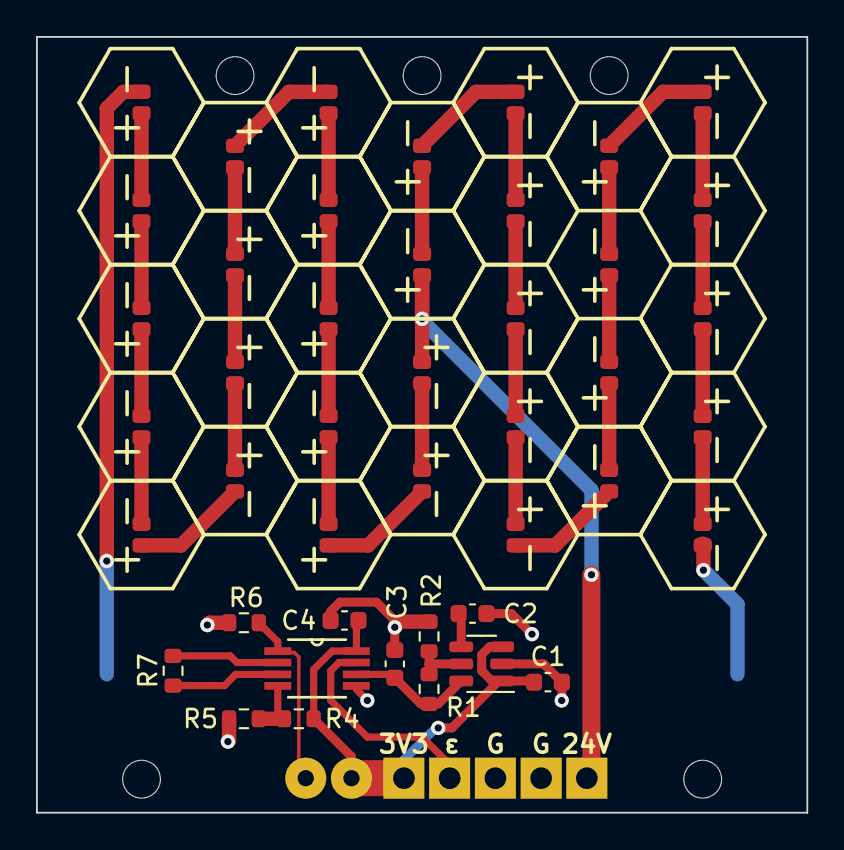
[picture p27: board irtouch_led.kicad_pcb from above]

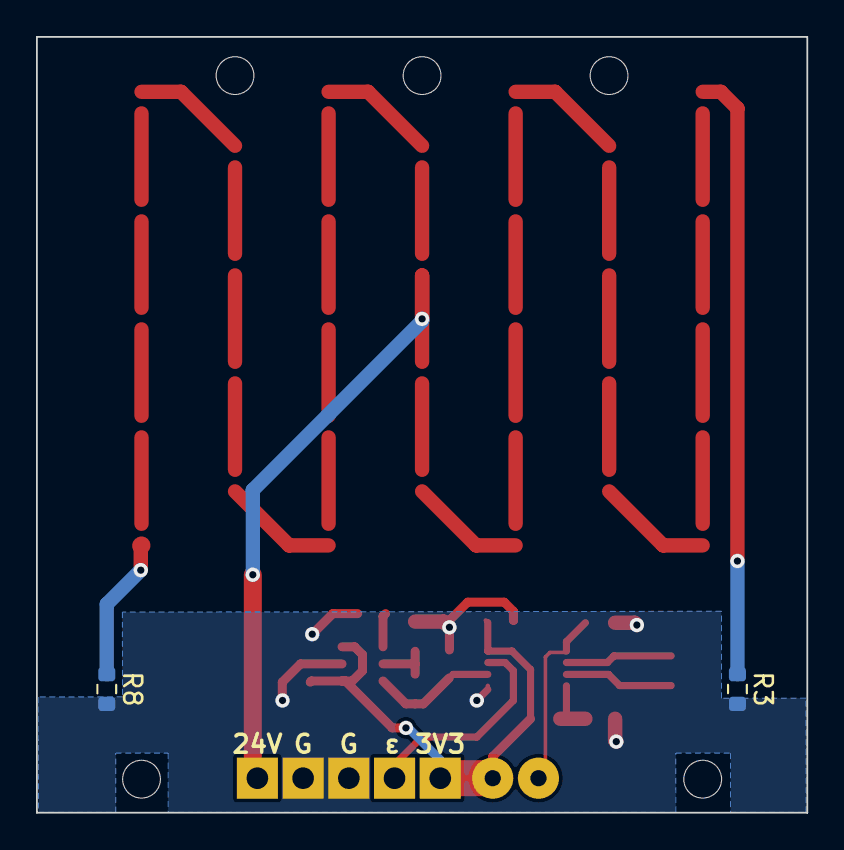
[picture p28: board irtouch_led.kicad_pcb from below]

Board: 2 copper layers, 42.8 x 43.1 mm, 50 parts (2 on the bottom side), 43 nets.

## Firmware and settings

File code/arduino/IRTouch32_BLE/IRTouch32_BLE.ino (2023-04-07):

/*  
 *  BEFORE FLASHING A PCB: 
 *  Make sure PCB_NAME is correct.
 */

#include <ArduinoBLE.h>
#include "IRTouch32.h"

#define SERIAL    false

#define PCB_NAME "IRTouch"
#define BLE_UUID_DATA_SERV      "ECBC" //16b UUIDs needed for compatibility with Blatann lib (python)
#define BLE_UUID_DATA_CHAR      "C134"

using namespace std;

BLEService dataService( BLE_UUID_DATA_SERV );
BLECharacteristic dataCharacteristic( BLE_UUID_DATA_CHAR, BLERead | BLENotify, NUM_DATA_VALUES, true );

uint8_t data[NUM_DATA_VALUES];

void setup() {
  for( int i = 0 ; i < 4 ; i++ ) {
    pinMode(read_pins[i], INPUT);
  }

  pinMode(MUX_IRTOUCH32_S0, OUTPUT);
  pinMode(MUX_IRTOUCH32_S1, OUTPUT);
  pinMode(MUX_IRTOUCH32_S2, OUTPUT);
  setupBleMode();
  if( SERIAL ) {
    Serial.begin(9600);
    while(!Serial);
    Serial.println("Setup complete");
  }
}

void loop() {
  BLEDevice central = BLE.central();
  if ( central ) {
    while ( central.connected() ) {
      if( central.rssi() != 0 ) {        
        readData();
        if( SERIAL ) { printData(); }
        dataCharacteristic.writeValue(data, NUM_DATA_VALUES);
      }
    }
  }
}

//=================== FUNCTIONS =====================\\

void readData() {
  for(int i = 0 ; i < NUM_DATA_VALUES/NUM_MUXS  ; i++ ) {
    selectIRTouchMuxOut(i);
    for(int analog_pin_idx = 0 ; analog_pin_idx < NUM_MUXS ; analog_pin_idx++ ) {
      data[measure_idx_to_grid_idx[i*NUM_MUXS + analog_pin_idx]] = analogRead(read_pins[analog_pin_idx])/4.0; // Normalisation to go from 10 bit to 8 bit
      //Serial.println(measure_idx_to_grid_idx[i*NUM_MUXS + analog_pin_idx]);
    }
  }
}

void printData() {
  Serial.println("");
  for(int i = 0 ; i < NUM_DATA_VALUES ; i++ ) {
    Serial.print(String(data[i]) + String(" "));
  }
}

bool setupBleMode() {
  if ( !BLE.begin() ) {
    return false;
  }

  // set advertised local name and service UUID:
  BLE.setDeviceName( PCB_NAME );
  BLE.setLocalName( PCB_NAME );
  
  BLE.setAdvertisedService( dataService );
  dataService.addCharacteristic( dataCharacteristic );
  BLE.addService( dataService );
  uint8_t zeros[NUM_DATA_VALUES] = {0};
  dataCharacteristic.writeValue( zeros, NUM_DATA_VALUES );
  
  BLE.advertise();

  return true;
}

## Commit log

2023-04-07 added arduino code, python code and pcb files
    [irtouch_led.kicad_pcb, irtouch_led.kicad_sch, irtouch_rcv.kicad_pcb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]
2023-04-09 added 3d files
    [IRTouch_led6_flex_thin.SLDPRT, IRTouch_led6_flex_thin.STL, IRTouch_led6_mechanical_interface.SLDPRT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]
2023-04-09 updated 3d files
    [IRTouch_flex.SLDPRT, IRTouch_flex.STL, IRTouch_flex_interface.SLDPRT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]
2023-04-11 updated 3D designs
    [Arduino_holder.SLDPRT, Arduino_holder.STL, WristCouplingAssembly.SLDASM]
2023-04-11 updated cad/3d/README.md
2023-04-12 added Arduino breakout pcb, updated irtouch_rcv design to 2-layer
    [ArduinoBreakout.kicad_pcb, ArduinoBreakout.kicad_sch, LM2576D2TR4-012G.step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]
2023-05-11 added assembly manual
2023-05-16 updated assembly manual
2023-05-18 finished assembly manuals
2023-05-29 Added PCB BOM
    [BOM.xlsx]
